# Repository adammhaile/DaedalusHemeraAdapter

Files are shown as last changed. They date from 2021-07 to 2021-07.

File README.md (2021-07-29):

# Daedalus Hemera Adapter Plate

This is a design for an aluminum adapter plate to mount an E3D Hemera onto the [Project R3D Daedalus](https://www.projectr3d.com/shop/p/daedalus) without any physical modifications to the printer itself.

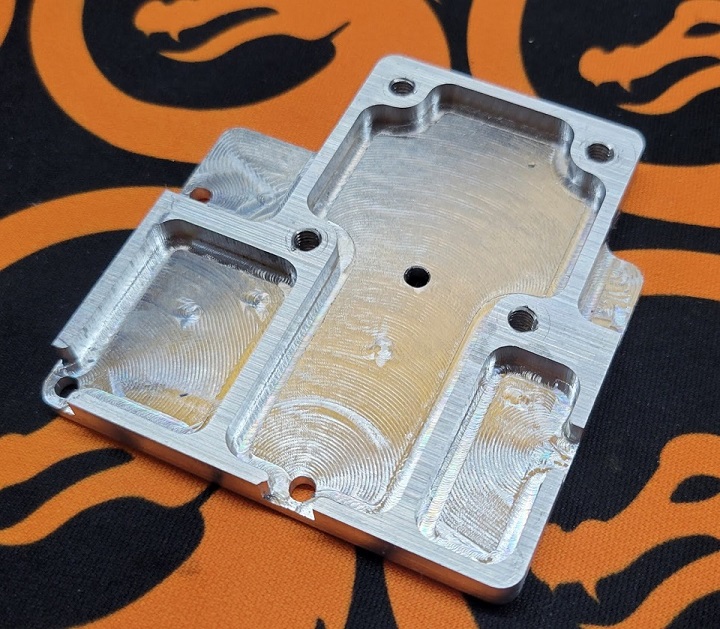
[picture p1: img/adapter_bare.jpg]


It bolts directly to the extruder carriage intended for a Bondtech BMG and, when using an E3D V6, will place the nozzle tip at the same Z offset. You will only need to change a few lines in the printer's `config.g` file.

The only real downsides are:

- Because the hemera is wider, you will lose about 10mm on the X axis, bringing the XY dimensions to 300x300mm. 
- The X position of the nozzle is shifted left compared to the stock extruder so items placed center bed in the slicer will actually be shifted left a bit when printed. This is fine since the bed itself is larger than 300x300mm - most print surfaces for the bed are 340x340. It simply means that things are shifted left of dead center on the bed, but still well within the usable area.
- When using the provided part cooling fan shround (which prevents any further X dimension loss), fan assembly can actually stick out the front of the machine a bit when at Y=0. Preventing the use of an enclosure that is flush with the front.
- This was designed for use with the standard V6 hotend. It is technically possible to use a volcano or other Hemera compatible hotend but you will need to find a solution to mount the Z probe lower.

## Required Components

You will need:

- The adapter plate itself. Note: this is **not** a printable item. It was designed to be milled from 1/4 inch or 6mm aluminum plate.
- 4x M4x8mm bolts, for mounting the adapter plate to the extruder carriage. 
- 4x M3x6mm bolts, for mounting the hemera to the adapter plate. Note, **do not** use anything longer than 6mm as it will break the Hemera!
- 4x M3x10mm bolts for mounting the part cooling duct to the hemera
- 2x M3x25mm bolts
- 2x M3 nuts
- 5015 radial blower fan rated for 24V
- 4-pin [Molex SL female](https://www.digikey.com/en/products/detail/molex/0050579404/115057) connector with appropriate crim connectors. See more below.
- E3D Hemera extruder and V6 hotend.

## Installation

As long as you replace the 5015 part cooling fan connector with the 4-pin Molex connector noted above, not modifications need to be made to the Daedalus itself other than pulling some of the cables through the chain a little more to provide some extra slack. 

First, print the provided [5015 fan mount](5015FanMount.stl) in a heat resistant material. PETG or ABS at a minimum but nylon or PC won't hurt.

Take the assembled Hemera and mount it to the adapter plate using the M3x6mm bolts with the completely flat side of the adapter facing the Hemera. Make sure the heater cartridge and thermister are mounted in the block so the wires are coming out the same side as the Hemera heatsink and fan.

Now mount the adapter plate to the Daedalus using the M4x8 bolts. Make sure they are good and tight.

You will need to replace the connector on the 5015 part cooling fan with the Molex SL connector. The stock Daedalus uses 2 part cooling fans, which is why it has 4 pins. Just make sure you match black and red between the connectors. It doesn't matter which you connect to.

Take the two M3 nuts and insert them into the hexagonal spots on the back of the part cooling duct. Use a couple small dabs of super glue on each to ensure they remain in place and give them a few minutes to dry.

Now attach the duct to the front of the hemera with the M3x10mm bolts.

Finally, use the M3x25mm bolts to attach the fan to the duct.

For wiring, follow the paths shown below.

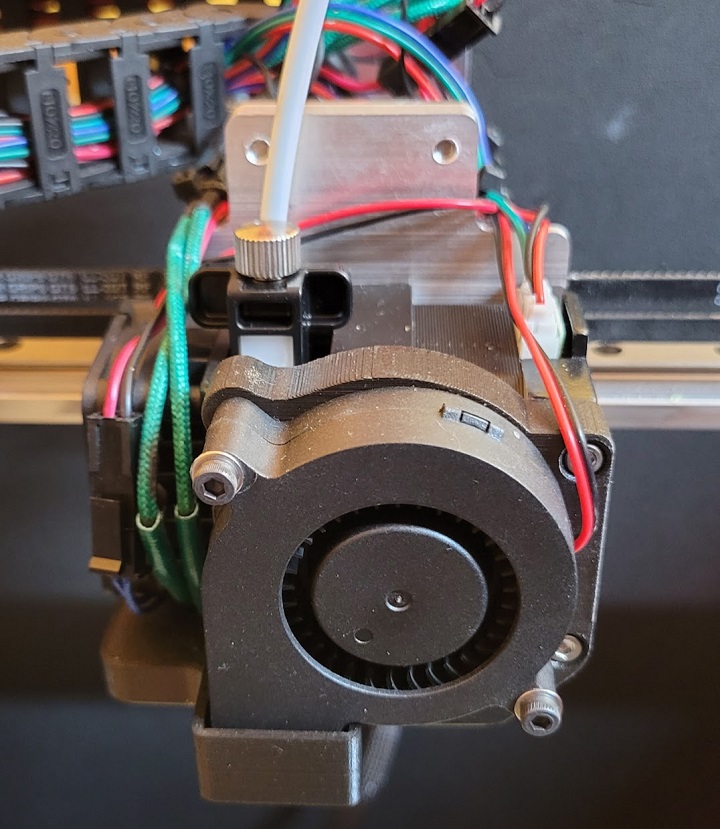
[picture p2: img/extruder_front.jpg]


There should be enough wire to reach everything but you may need to remove the back of the Daedalus and feed some extra wiring (especially for the extruder motor) through the cable chain. The connector from the Bondtech motor should plug right into the Hemera with no issues.

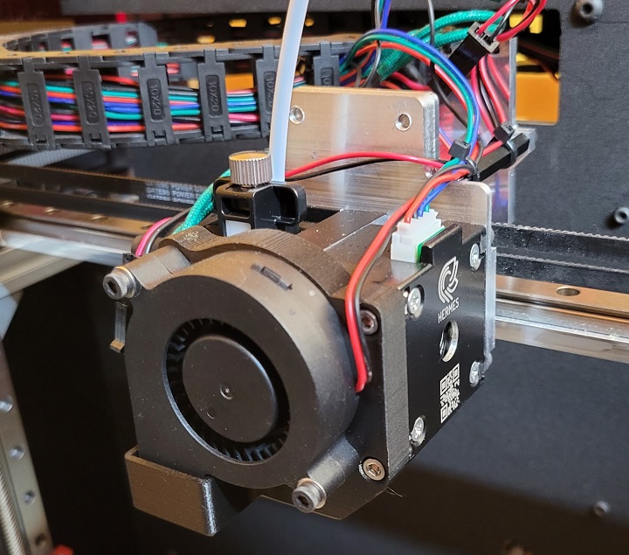
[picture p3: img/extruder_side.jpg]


Provide some strain relief with some zip ties as show and you are done! Now on to the config...

## Configuration Updates.

This part is easy, just a few things to tweak. Load Duet Web Control for your Daedalus and open up `config.g`. Note, just worry about the values called out here. Leave any other non-extruder related values in the lines mentioned the same!

First, look for the motor currents line and change the extruder value to between 800 and 1200mA. I used 1100mA:

`M906 X1600 Y1600 Z1200 E1100 I60`

Change your axis max distance for X to 300mm:

`M208 X300 Y300 Z345`

Now update your steps/mm for the extruder to me 409:

`M92 X200 Y200 Z800 E409`

Next, you need to change your Z probe offset to `X8.75 Y62.45` to reflect the different position of the nozzle to the Z probe, for mesh leveling. You will want to come back to this line later when you calibrate your Z probe height offset. It will likely be close to what you had before, but best to get it right!

`G31 X8.75 Y62.45 Z2.6 P25`

That's it! Save the config and let the printer restart.
Once it's back online, I highly recommend running a PID autotune since it's a different hotend. Just in case.

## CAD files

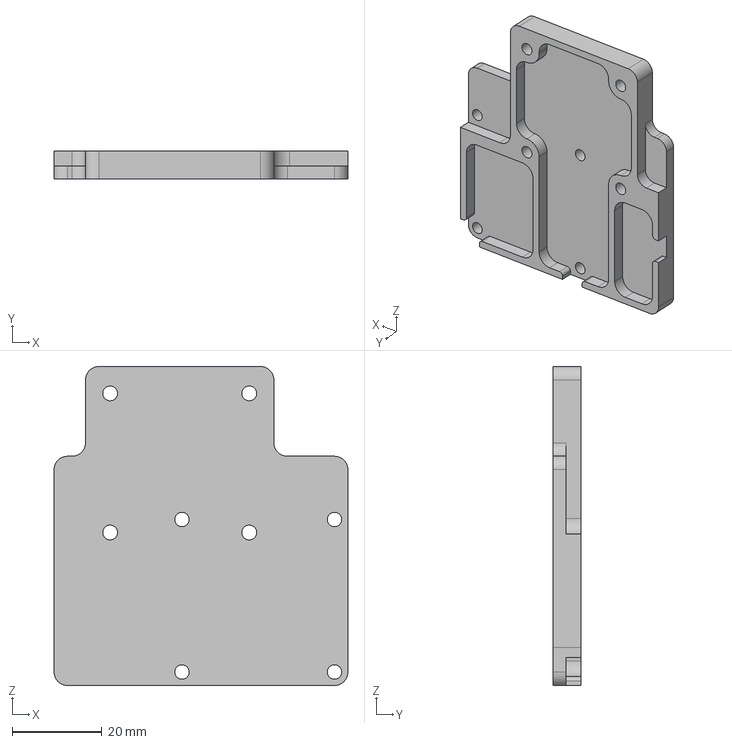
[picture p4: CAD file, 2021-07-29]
AdapterPlate.step
65.5 x 6.35 x 71.1 mm

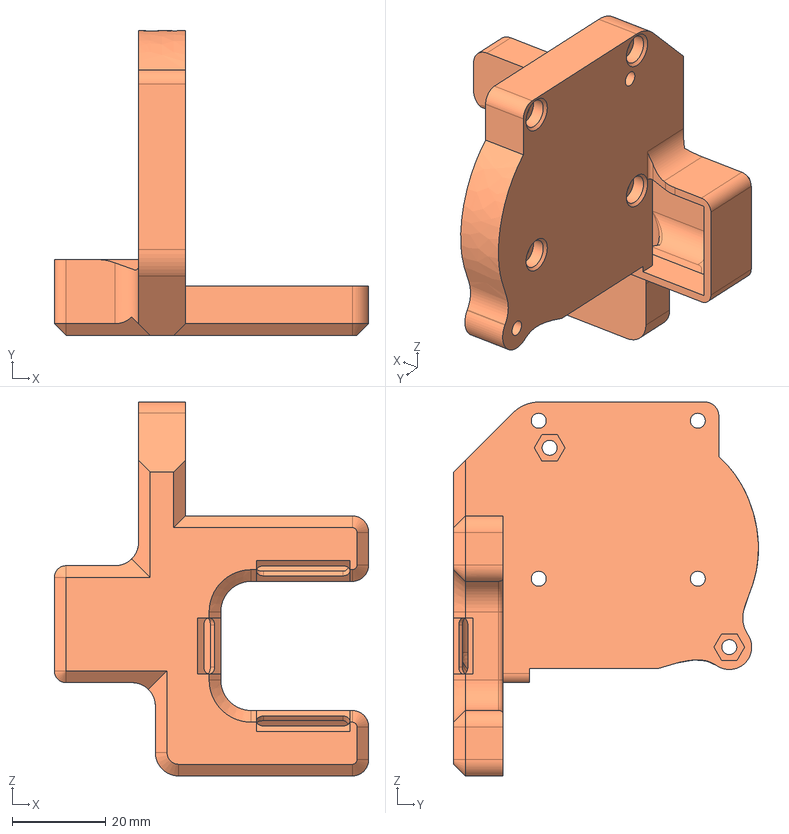
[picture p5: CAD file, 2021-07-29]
5015FanMount.step
67.2 x 65.2 x 79.9 mm

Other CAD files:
5015FanMount.3mf
5015FanMount.stl
